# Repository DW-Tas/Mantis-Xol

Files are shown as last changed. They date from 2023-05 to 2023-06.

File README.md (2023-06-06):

# Mantis Xol 2


## Description
Originally a project to slap 5020 blower fans onto Mantis, this toolhead variant started as an attempt to improve parts cooling, spurred on by Derpimus' noted cooling woes on his DOOMCube. After finding that the 5020s were just plain too fat to fit without looking like a standard Ender 3 Thingiverse special, I abandoned the large fan dream in favor of better cooling efficiency and lighter weight. This new and improved dream was also corrupted by my then budding and now all-consuming love for worm gears.

Join me on Discord (https://discord.gg/armchairengineeringsux)

## New Features for Xol 2
 - Cooler: Still a little ugly but better
 - Lighter: 260g-ish for Sherpa Mini
 - Rigid-er: I want to throw this thing across the room

#### Features:
 - Better airflow than Stealthburner (6-7 CFM through short ducts vs 4.6-5.2 CFM through long ducts)
 - Improved resonance management compared to Mantis 5015
 - Support for Sherpa Mini-pattern extruder mounting as well as Annex Engineering's **Double Folded Ascender** worm gear extruder
 - Support for JosAr's Klicky, VinnyCordeiro and WhoppingPochard's PCB Klicky, and Nionio6915's Euclid
 
#### Supported (incl. usermods/experimental):
|Hotends |Extruders |Probes |
|--- |--- |--- |
| Rapido HF | Sherpa Mini | VoronDesign's TAP |
| Dragon SF/HF | Orbiter 2 | Beacon (normal) |
| Revo Voron | Vz-hextrudort | (PCB) Klicky |
| Phaetus XG | DropEffect | Euclid |
| Bambulab | LGX Lite |--- |
| Dragon UHF Mini / NF Crazy |--- |--- |
 
#### Future Development (No ETA):
 - Bracing for PCB mounts
 - Quickdraw 2 support
 - Update DFA Bottom to latest version for slightly better heatset quality of life
 - Port nozzle LEDs to Xol 2 (see usermods)
 - Port MMU sensor support to Xol 2
 - Confirm fitment for MattTheBaker's Beacon

## Build Notes:
This toolhead might require other modifications to retain full functionality of your printer. 
 - All test machines used for this mod had Rama's front idlers which have a much lower profile compared to stock Voron front idlers. The fan assemblies might conflict and reduce usable X travel.
 - The Klicky Probe carriage that was adapted was originally designed for the Dragon hotend. You'll need to use a taller probe body to reach the bed such as the one used by [Unklicky BFP](https://github.com/majarspeed/Unklicky). *This isn't an issue for Euclid or PCB Klicky*.
## Bill of Materials 
|Item|Count|Note|
|----|-|--|
|Rapido or XG|1|
|4010 24v blower fans|2|Add Polulu 3796 if you want the fancy 12v Deltas|
|2510 24v axial fan|1|
|M2x8 SHCS|2|
|M2x12 SHCS|4|
|M2x20 SHCS|2|
|M2.5x20 SHCS|4|
|m3x6 BHCS|7|
|m3x8 BHCS|7|
|m3x20 SHCS|2|
|M2 Heatset 4L x 3.5 OD|11|
|M3 Heatset "Standard"|10|
|D2F-5L Microswitch|1|
|M2x8 or M2x10 Self-Tapping|1|Optionally 1 more M2 heatset and an M2x8 SHCS|
|6x3 magnets|3|
|ZIP TIES||
## Changelog
### 29 November 2022 - Beacon Support
- Release Day means Beacon Support. Find it in the Experimental folder.
### 27 November 2022 - Tap Support
- Release Day means Tap Support. Find it in the Experimental folder.
### 22 November 2022 -Revo Voron
- Added support for Revo Voron with the Sherpa Mini Hotend mount
### 10 November 2022 - Shiny shiny
- Added nozzle LED support. Find it in the Experimental folder.
### 23 October 2022
### 3 October 2022 - Xol 2
- Improved aesthetics
- Downsized HE fan to 2510
- No more self-tapping screws
- Added front brace for Sherpa Mini
- New ducts for Tridents with lead screws
- Miscellaneous printability improvements
### 3 Aug 2022 - Xol with Boots
- Added MGN9H carriages for PCB Klicky
- Added additional stabilization for ducts. Ideally, these are fastened with 2x M2x20 and M2 heatset inserts.


## Acknowledgement
[Long/Mandryd](https://github.com/mandryd/VoronUsers/tree/master/printer_mods/Long/Mantis_Dual_5015) for the Mantis toolhead.<br/>
[TheWarolf](https://github.com/TheWarolf/Voron-Personal-Mods/tree/main/V2/Long_Mantis_Toolhead) for the ERCF sensorized Hotend Mount.<br/>
[Derpimus](https://github.com/lraithel15133) for the exegesis, some CAD work, feedback, and just being a rad dude.<br/>
[KayosMaker](https://github.com/KayosMaker) for the MGN12 Klicky X-Carriage and CAN board mounts and spacers.<br/>
[JosAr](https://github.com/jlas1/Klicky-Probe) for Klicky.<br/>
[WhoppingPochard](https://github.com/tanaes) and [VinnyCordeiro](https://github.com/VinnyCordeiro/) for PCB Klicky.<br/>
[Nionio6915](https://github.com/nionio6915/Euclid_Probe) for Euclid. <br/>
[VoronDesign](https://github.com/VoronDesign) for this particular CoreXY flavor.<br/>
[AnnexEngineering](https://github.com/Annex-Engineering) for the Sherpa Mini and Double Folded Ascender extruders, and the K3 that influenced the air management of the ducts. And also for giving access to an early revision of the new DFA so it could be adapted for this toolhead.<br/>
[Clee](https://github.com/clee), you know what you did.  
[Takuya](https://github.com/T4KUUY4)... just added the 36mm SB2040 mount

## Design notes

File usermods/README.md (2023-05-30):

# Community Xol mods

---

|Creator |Mod title |Description |
|--- |--- |--- |
|Derpimus |Dragon Hotend |Adds Dragon SF/HF hotend support for Sherpa [TAP/No-TAP] |
|PrintStructor |BambuLabs Hotend |Adds BambuLabs hotend support for Sherpa [TAP/No-TAP]. Supports 2510 and 3010, also LEDs |
|T4KUUY4 |SB2040 36mm Mount |Adds mount to hold SB2040 board to sherpa |
|DW-Tas |SB Led Mod |Adds support to reuse your SB LEDs for a decretive LED logo on the hotend mount |
|DW-Tas |Xol 2 Hotend Mounts - Orbiter v2 |Adds support for Orbiter v2 extruder |
|DW-Tas |Xol 2 Hotend Mounts - VX-Hexdrudort-Low |Adds support for VZ Hextrudort and LGX lite extruders |
|DW-Tas |Xol Carriage |**Experimental: Carriage for Xol using Voron Design CW2 mounting pattern** |
|iniqy | Dragon hotend | Adds Dragon SF/HF/UHF/Crazy hotend support for VZ Hextrudort + LGX Lite Extruders (print with a Sherpa carriage) [TAP/No-TAP] |
|KayosMaker| Klicky dock and mount | can be found in the MantisUsermods repo [here.](https://github.com/mandryd/MantisUsermods/tree/main/Usermods/KayosMaker/MGN12_Klicky/STLs) |
|KayosMaker| EBB36 and SHT36 Mounts for No-TAP Carriages | Mounts to carriage and can optionally tie in to Sherpa or VZHextrudort with a standoff. See repo linked below for printable standoffs. |
|KayosMaker| EBB36 and SHT36 Universal Mounts | Mounts to extruder motor screws via standoffs. Standoffs included that can be used for above mount, once gap is measured.  External repo [here.](https://github.com/KayosMaker/CANboard_Mounts) |

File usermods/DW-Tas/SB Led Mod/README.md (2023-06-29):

# LED mounts for Xol 2 using standard LED harness from Stealthburner

render

This mod uses the stock LED harness from Voron Stealthburner to add status and nozzle lights to Xol 2.

Depending on your build you will probably need a three wire extension between the Stealthburner LED harness and your toolhead board or standard wire harness.

There are now two versions to choose from. v1 is as per the render above. V2 is more compact and allows access to the bottom screw in the K-Plate if you use Sherpa Mini.

v2 render

## What to print?
Print the ducts that suit your build. Standard or TAP availble for normal lenght or UHF length ducts are available

Print the faceplate parts for the version you want.
Both versions support neopixel and rainbow barf options.
Both versions require faceplate parts 1 & 2 and a diffuser to suit.
v1 requires an extra logo plate to be printed.

I recommend printing all of the faceplate parts, and diffuser parts in 0.1mm layer height 0.25 first layer will work fine.
Ducts can be printed the same as for standard Xol 2 ducts. Smaller layer heights may give you smoother walls on your ducts. I used 0.15mm layers.

## Assembly
This section is a work in progress.
for v2, standard neopixel versions, it works well to glue the white diffuser into the faceplate 1 part with a tiny drop of super glue.

## Wiring

Wires route under either side of the Xol 2 (behind a fan) and accross the 1st part of the faceplate where the status LED is inserted. Then behind the other fan before going down to the first duct. Then back accross to the other side under the 25mm hotend cooling fan behind the faceplate parts to the other duct. Look at the pictures below 😎

***Alternate wiring for non-UHF version.
You can put the 1st LED into the duct on the side all your wires go to first, then insert the 2nd LED into the "Status LED" location, and finally, the 3rd LED goes down to the other duct. If you insert the LEDs in this order, you will have to update your LED .cfg to make sure that the status LED is index #2 and that the others are index 1 and 3.

wiring1

wiring2

The cutout behind the updated front faceplate leaves space for the wires routed above the 25mm hotend cooling fan.

wiring3

Only the front faceplate parts and ducts are changed from the standard hotend mounts and it uses the same m2 heatsets that would be used for stock Xol 2.

cad1

cad2
<br/>
<br/>
<a href="https://www.buymeacoffee.com/dw.tas" target="_blank">Buy Me A Coffee</a>

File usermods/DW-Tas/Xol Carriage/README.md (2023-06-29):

# PRE-ALPHA EXPERIMENTAL
## Xol Carriage
A new carriage built to allow Xol to standardise around the Voron CW2 (TAP) mounting pattern.
This is in very early stages of development. Parts are subject to change at any time.
Testing and feedback are welcome at the Xol-Toolhead channel on the Armchair Engineering discord. <https://discord.com/channels/1029426383614648421/1046422202460930129>

### Design Goals
* Uses same mounting pattern as TAP (reduce Xol permutations)
* Easily remove toolhead from carriage without toolhead dissassembly
* Modular approach to probes

### Additional Hardware
To accomodate design requirements, some additional hardware will be required when using this mount.
Specifically, M2.5 heatsets are used in the feet of the Xol hotend mount.

The dimentions of the heatests are
* thread: M2.5
* Lenght: 4mm
* Outer Diameter: 3.5mm
(M2.5x4x3.5)

### Acknowledgements
Thanks to the Armchair Engineering team and Voron Design. This carriage is built for Xol but is based heavily on the Voron Design CW2 mounting system.
<br/>
<br/>
<a href="https://www.buymeacoffee.com/dw.tas" target="_blank">Buy Me A Coffee</a>

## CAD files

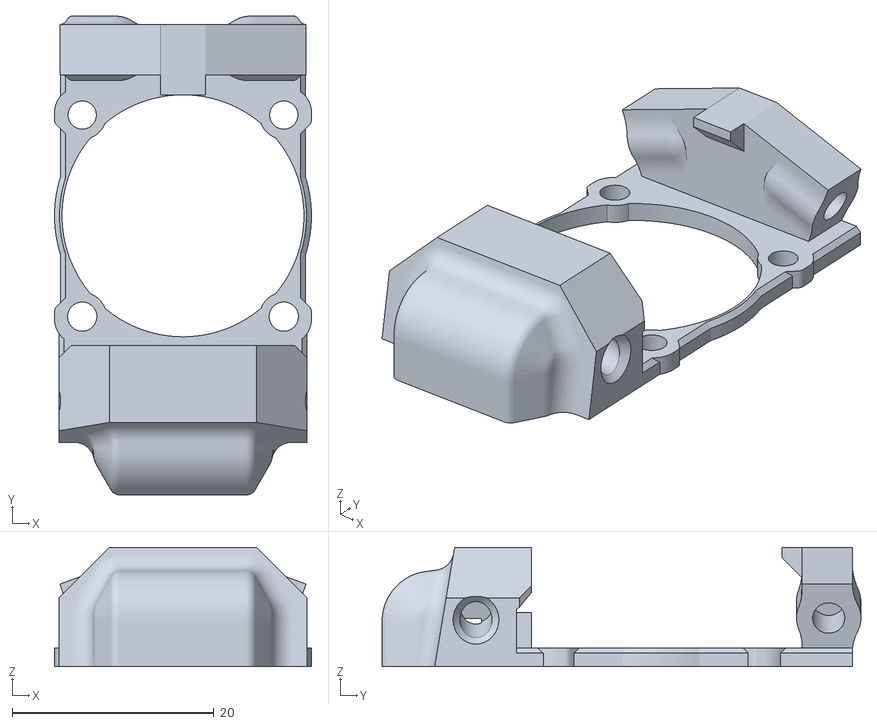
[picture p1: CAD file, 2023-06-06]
usermods/DW-Tas/SB Led Mod/STL/v2 faceplates/Faceplate - XG 1 - BARF - v2.stl
25.5 x 47.5 x 11.8

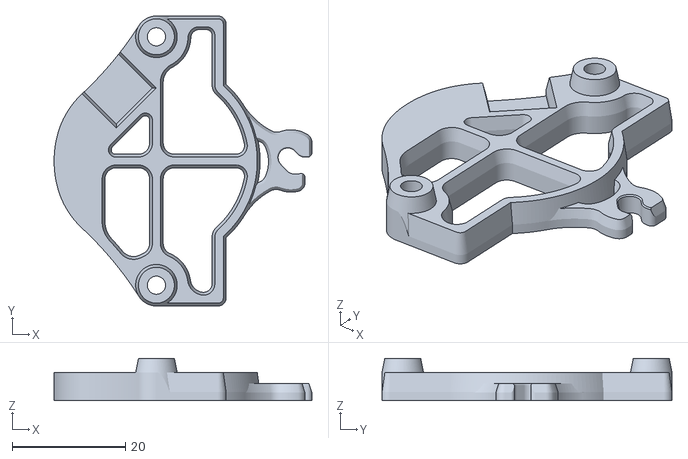
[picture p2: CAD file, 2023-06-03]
usermods/DW-Tas/Xol Carriage/STL/EBB Mounts/EBB Mount - SHT36 - Sherpa Mini - Xol Carriage.stl
45.5 x 51.2 x 7.50

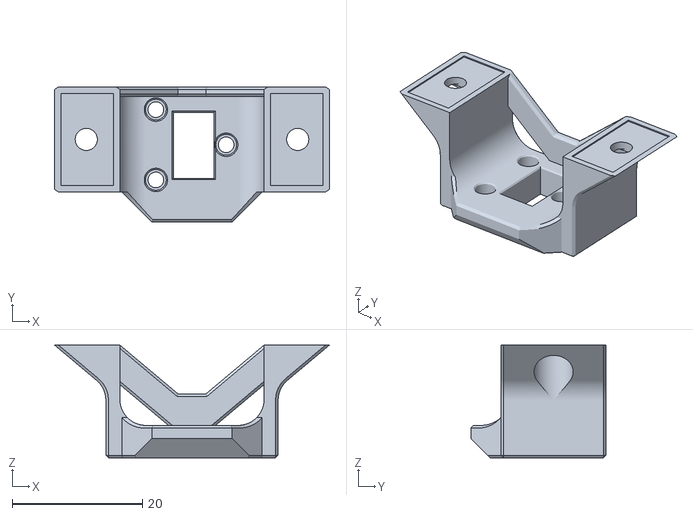
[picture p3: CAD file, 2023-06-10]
usermods/DW-Tas/Xol Carriage/STL/Probe Modules/Klicky_PCB_Module_UHF.stl
42.3 x 20.8 x 17.3

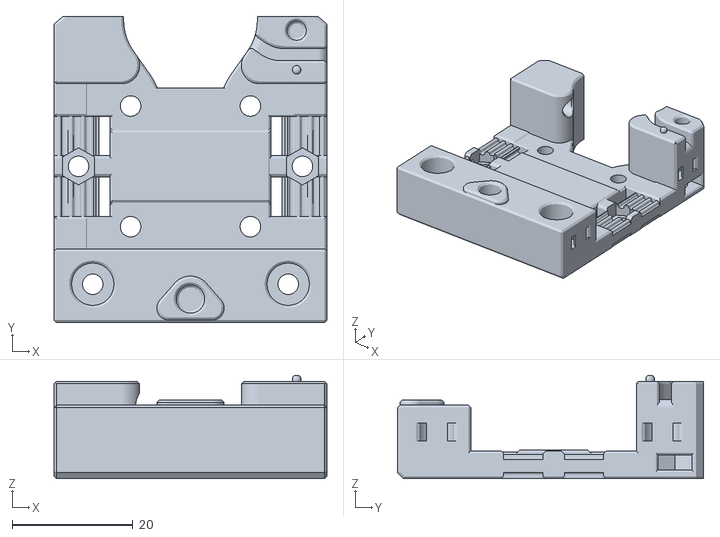
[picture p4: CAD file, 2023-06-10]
usermods/DW-Tas/Xol Carriage/STL/Xol_Carriage_Rear.stl
45.3 x 50.7 x 17.2

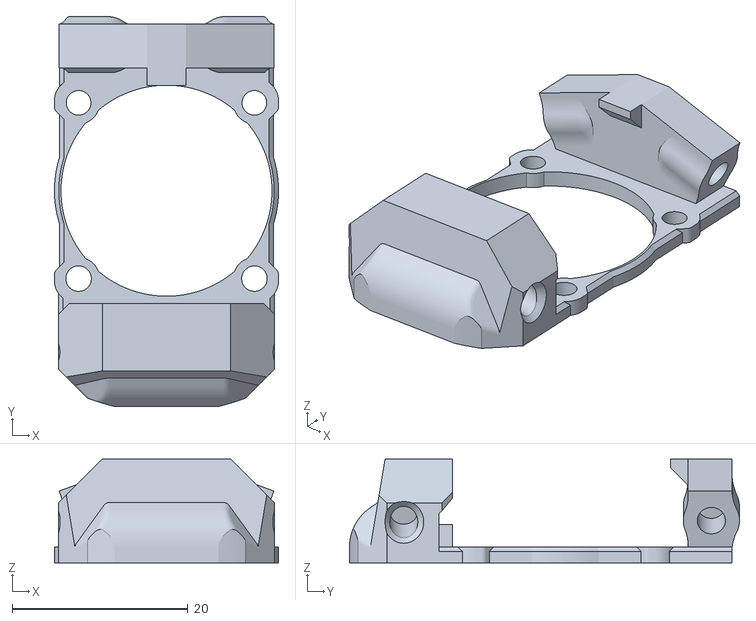
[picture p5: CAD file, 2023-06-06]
usermods/DW-Tas/SB Led Mod/STL/v2 faceplates/Faceplate - XG 1 - LED - v2.stl
25.5 x 44.4 x 11.8

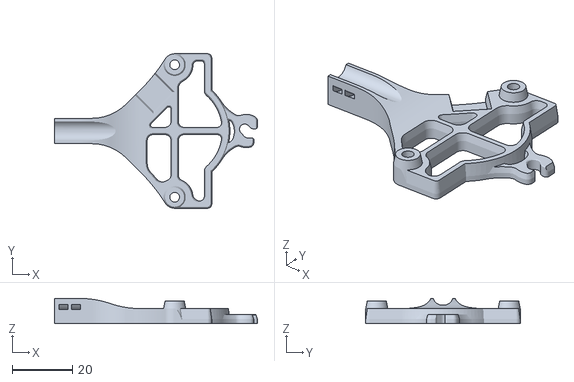
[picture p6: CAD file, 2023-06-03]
usermods/DW-Tas/Xol Carriage/STL/EBB Mounts/EBB Mount - SHT36 - Sherpa Mini - Xol Carriage [strain relief].stl
67.2 x 51.2 x 8.36

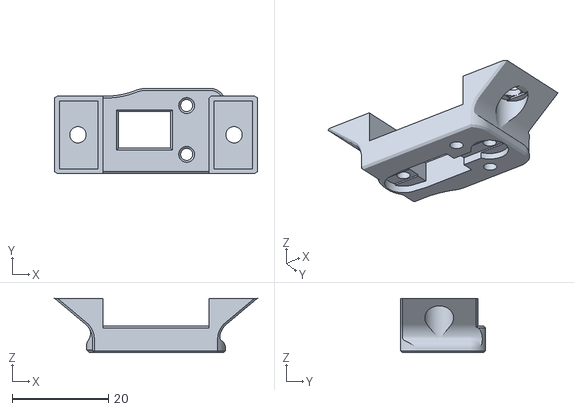
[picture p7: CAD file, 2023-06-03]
usermods/DW-Tas/Xol Carriage/STL/Probe Modules/Euclid_Module_90.stl
42.3 x 17.7 x 11.3

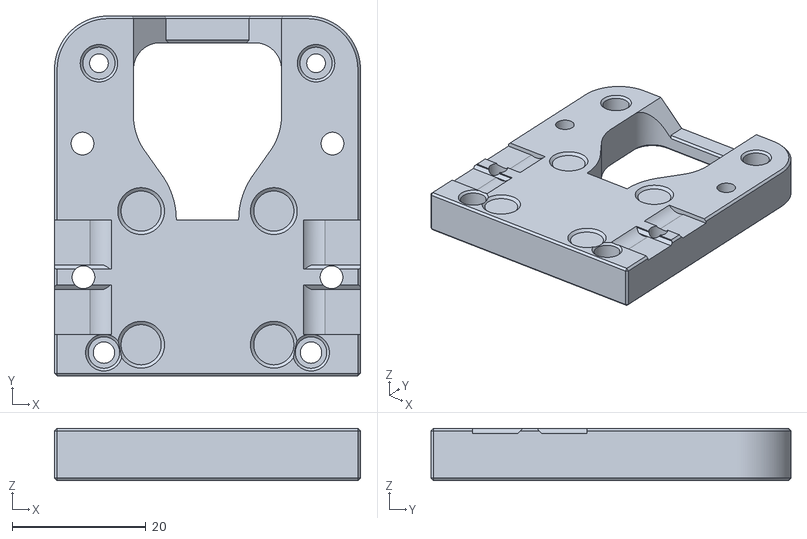
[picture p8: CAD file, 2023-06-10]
usermods/DW-Tas/Xol Carriage/STL/Xol_Carriage_Front.stl
45.8 x 53.9 x 7.84

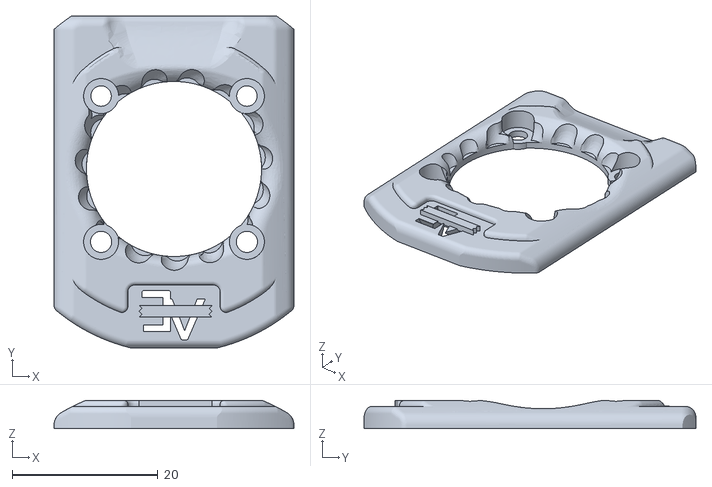
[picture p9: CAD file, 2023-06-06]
usermods/DW-Tas/SB Led Mod/STL/v2 faceplates/Faceplate - Front - LED v2 [Southern Hemisphere Edition].stl
32.9 x 45.5 x 3.89

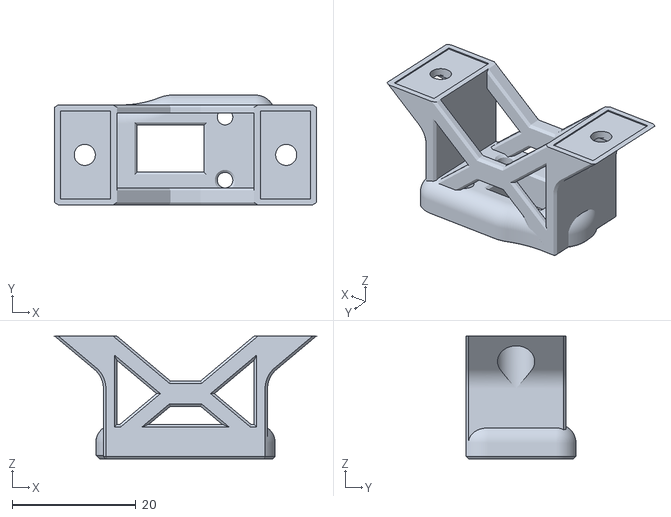
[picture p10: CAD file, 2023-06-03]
usermods/DW-Tas/Xol Carriage/STL/Probe Modules/Euclid_Module_90_UHF.stl
42.3 x 17.7 x 19.8

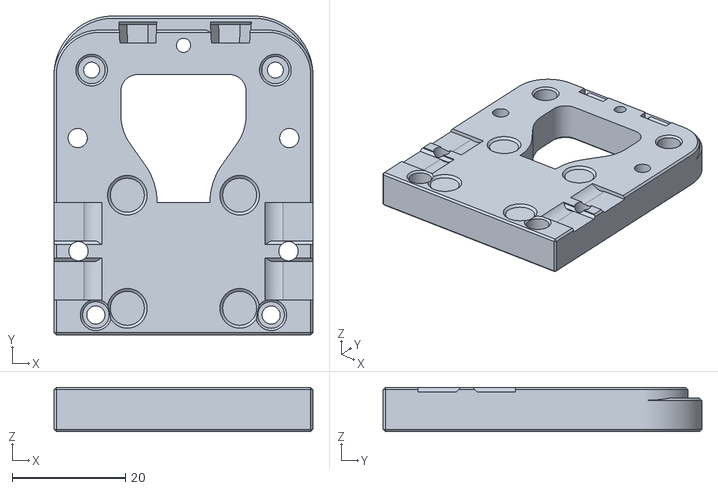
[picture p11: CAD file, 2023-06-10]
usermods/DW-Tas/Xol Carriage/STL/Xol_Carriage_Front_KlickyNG.stl
45.8 x 56.3 x 7.84

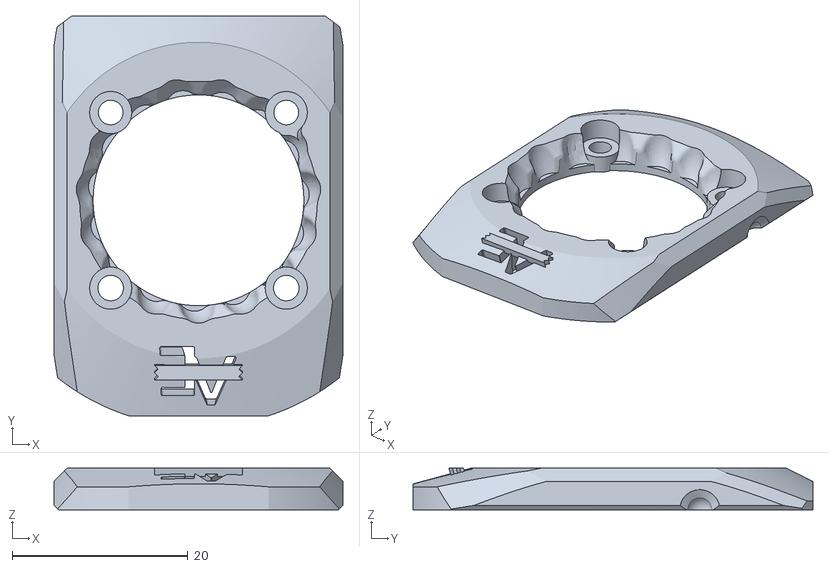
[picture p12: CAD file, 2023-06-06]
usermods/DW-Tas/SB Led Mod/STL/v2 faceplates/Faceplate - Front - LED v2.stl
32.9 x 45.5 x 4.73

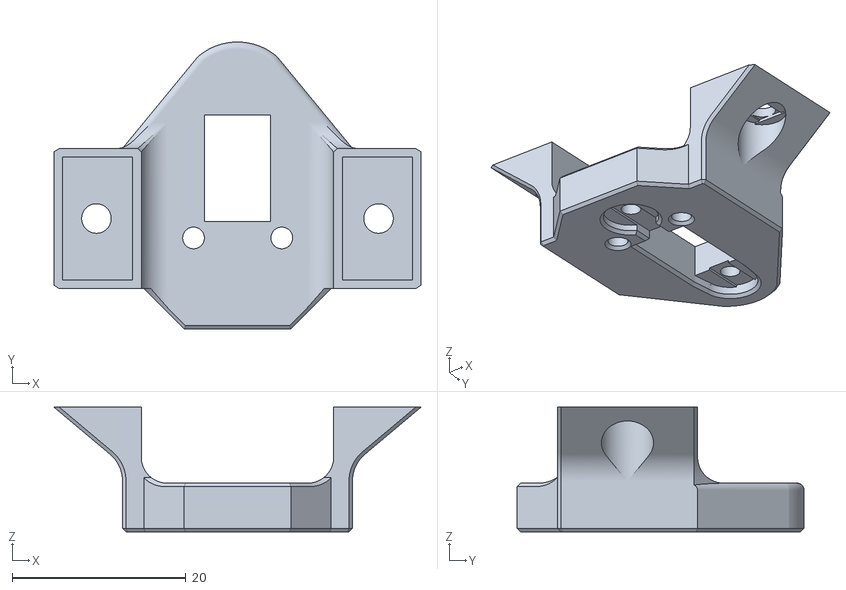
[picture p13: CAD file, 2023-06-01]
usermods/DW-Tas/Xol Carriage/STL/Probe Modules/Euclid_Module.stl
42.3 x 33.0 x 14.3

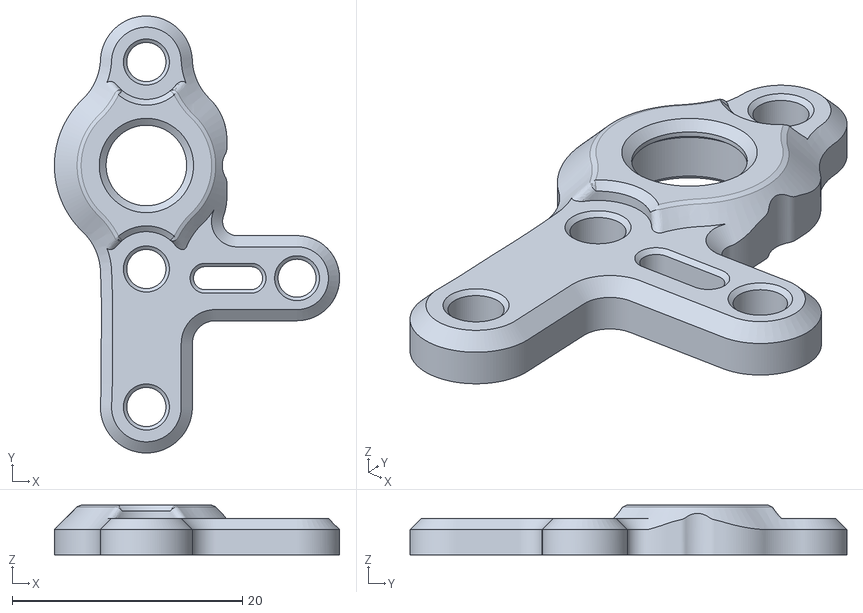
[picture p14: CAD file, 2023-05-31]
usermods/DW-Tas/Xol Carriage/STL/Sherpa_housing_front_Xol_carriage_k (RIDGA 3mm).stl
24.8 x 38.0 x 4.33

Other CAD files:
usermods/DW-Tas/SB Led Mod/STL/v2 faceplates/Faceplate - Front - BARF v2.stl
usermods/DW-Tas/Xol Carriage/STL/Probe Modules/Beacon_Module_PCB_support_UHF.stl
usermods/DW-Tas/Xol Carriage/STL/Sherpa_housing_front_Xol_carriage_k.stl
usermods/DW-Tas/SB Led Mod/STL/v2 faceplates/Faceplate - XG - fan spacer.stl
usermods/DW-Tas/Xol Carriage/STL/Adapter Orbiter2 - Xol Carriage.stl
usermods/DW-Tas/Xol Carriage/STL/Adapter Sherpa Mini - Xol Carriage.stl
usermods/DW-Tas/Xol Carriage/STL/Adapter VZ-Hexdrudort-Low - Xol Carriage.stl
usermods/DW-Tas/Xol Carriage/STL/Probe Modules/Beacon_Module.stl
usermods/DW-Tas/Xol Carriage/STL/Probe Modules/Beacon_Module_PCB_support.stl
usermods/DW-Tas/Xol Carriage/STL/Probe Modules/Beacon_Module_UHF.stl
usermods/DW-Tas/Xol Carriage/STL/Probe Modules/KlickyNG_Module.stl
usermods/DW-Tas/Xol Carriage/STL/Probe Modules/Klicky_Module.stl
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

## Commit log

2023-05-30 Create Xol Carriage mod
    [Beacon_Module.stl, Beacon_Module_UHF.stl, KlickyNG_Module.stl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]
2023-05-30 Added Adapter plate STLs
    [Adapter Orbiter2 - Xol Carriage.stl, Adapter Sherpa Mini - Xol Carriage.stl, Adapter VZ-Hexdrudort-Low - Xol Carriage.stl]
2023-05-30 Added PCB support for Beacon Mounts
    [Beacon_Module_PCB_support.stl, Beacon_Module_PCB_support_UHF.stl, Xol_Carriage_Prototype_beacon_bits.step]
2023-05-31 added K-Plates
    [Sherpa_housing_front_Xol_carriage_k (RIDGA 3mm).stl, Sherpa_housing_front_Xol_carriage_k.stl]
2023-06-01 Added Euclid module and arranged modules folder
    [Beacon_Module.stl, Beacon_Module_PCB_support.stl, Beacon_Module_PCB_support_UHF.stl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]
2023-06-03 EBB Mounts for sherpa mini
    [EBB Mount - SHT36 - Sherpa Mini - Xol Carriage [strain relief].stl, EBB Mount - SHT36 - Sherpa Mini - Xol Carriage.stl]
2023-06-03 Added Euclid Module 90
    [Euclid_Module_90.stl, Euclid_Module_90_UHF.stl]
2023-06-06 Create Xol LED XG fan spacer.stl
    [Xol LED XG fan spacer.stl]
2023-06-06 LED Mod XG update
    [Faceplate - Front - BARF v2.stl, Faceplate - Front - LED v2 [Southern Hemisphere Edition].stl, Faceplate - Front - LED v2 [voron].stl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]
2023-06-06 Create Faceplate - XG 1 - BARF - v2.stl
    [Faceplate - XG 1 - BARF - v2.stl]
2023-06-06 Create Xol 2 - Stealthburner LED v2.step
2023-06-10 Updated carriage body parts
    [Xol_Carriage_Front.stl, Xol_Carriage_Front_KlickyNG.stl, Xol_Carriage_Rear.stl]
